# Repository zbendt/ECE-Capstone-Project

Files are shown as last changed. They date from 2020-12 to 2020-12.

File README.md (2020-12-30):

# ECE44x_Senior_Design
ECE 441 - 443 Project folder with files for senior capstone project for Jorian Bruslind, Mack Hall, and Zach Bendt

Brief descriptions of each member's responsibilities are detailed here. Below is a list of main projects for each team: 

- [**Electrical**](https://github.com/Jbruslind/ECE44x_Senior_Design/tree/master/Electrical)
	- [Stepper Driver PCB](https://github.com/Jbruslind/ECE44x_Senior_Design/tree/master/Electrical/Auxiliary%20Stepper%20Driver%20PCB)

	- [Central Processor PCB](https://github.com/Jbruslind/ECE44x_Senior_Design/tree/master/Electrical/Central%20Procesing%20PCB)

	- [Vaccumn Pump Controller](https://github.com/Jbruslind/ECE44x_Senior_Design/tree/master/Electrical/Vacuum%20Pump)

- [**Mechanical**](https://github.com/Jbruslind/ECE44x_Senior_Design/tree/master/Mechanical) 
	- [Custom Mechanical Parts/Models](https://github.com/Jbruslind/ECE44x_Senior_Design/tree/master/Mechanical/Project%20Model%20Files/Inventor%20Files/Custom_Delta)
	
	- [PCB Modeling](https://github.com/Jbruslind/ECE44x_Senior_Design/tree/master/Mechanical/Delta%20Robot%20Arm)
 
- [**Computer Science**](https://github.com/Jbruslind/ECE44x_Senior_Design/tree/master/Computer%20Science)
	- [Main Program](https://github.com/Jbruslind/ECE44x_Senior_Design/tree/master/Computer%20Science/MircobialAnalysisTool)
	
	- [GRBL Code](https://github.com/Jbruslind/ECE44x_Senior_Design/tree/master/Computer%20Science/GRBL%20Code)

Automated Microbial Analysis 

The Automated Microbial Analysis project aims to develop a system which is able to analyze a series of microbial samples on a special media 
called PetriFilm automatically. PetriFilm is a 3M product that is used in a variety of scientific capacities, mainly in food science and the medical field. 

<!---![PetriFilm](https://github.com/Jbruslind/ECE44x_Senior_Design/blob/master/Research/Petrifilm.jpg){ width=50% }-->


PetriFilm is a very thin paper-like substance which has 2 layers: on one there is an agar media film that is used to grow bacterium, 
on the other there is a wax coating that is used to seal the sample from outside interference. A liquid sample can be applied to this 
agar film and left to incubate over a period of 1 - 2 days. After this time, the bacteria that were present within the sample will have 
 had enough time to grow into colonies which are visible to the human eye. These colonies can be counted and the original number of bacterium 
 per unit volume can be known from the original sample. The process to count the bacteria samples and categorize them into datasets is often 
 tedious and can take a human operator around 1 - 2 minutes per sample. With sample sizes of 50 - 60, this process 
 can easily take over an hour. The goal of our project is to use an automated system to count these bacteria colonies in sample sets of upwards 
 of 100+ in as little as 20 minutes. This data will be automatically stored and tabulated within the client's original database. 

Being a robotics project there are inherent complexities that must be resolved between subgroups such as the electrical control of the mechanical design, 
computer commands for electrical control and how effective the mechanical design facilitates the overall process. With that, the project must maintain 
a high level of communication and simplicity so that all groups are able to understand how their design affects the overall system and others work.

### Mechanical Sub-System 

The mechanical sub-system was designed using industrial examples of delta robots in mind and special attention paid to the accuracy, speed, and cost of 
the system. Arguably, the most important aspect of our project is that is must be accurate so as not to damage the provided samples 
and to improve it's overall time cost for this process (less mistakes mean less time needed to recover). The delta robot design was made using 
many commercial off the shelf (COTS) parts with a few custom designed parts that were manufactured using a 3D printer (the Creality Ender 3 .4mm to be precise). 



### Electrical Sub-System 

The system interacts with the samples to be tested via an end-effector that is moved by three stepper motors in a delta configuration. 
The goal of the Electrical Sub-System is to enable these interactions to happen at the command of the Computer Science Sub-System. The 
stepper motors are being controlled via an ATmega 328 microcontroller. The microcontroller is running specialized software which translates 
coordinates sent from a Raspberry Pi into waveforms representing the direction, distance, and speed a motor should move in. These waveforms 
are then passed to a stepper driver, which switches power to the motor according to the information within these waveforms. The end result is a 
stepper motor which can be controlled via a Raspberry Pi. An additional ATmega 328 microcontroller is utilized to control the other electrical aspects 
of the system as well. Such duties include enabling and disabling the vacuum pump, as well as enabling and disabling the flash for the system camera.

### Computer Science Sub-System
<p align="middle">
              
</p>
The computer science sub-system has three primary functions: automation control, computer vision image analysis and user interface.
 All three of these functions are implemented on the RaspberryPi microcontroller. The user interface was created using PyQT and is used to input various pieces of data 
 such as how many samples are to be analyzed and also where the user starts/stops/resets the analysis process. The user interface is updated
 throughout the process and displays the current sample image as well as relevant data about the sample. The automation controls are calculated 
 by the RaspberryPi which then sends the control messages via serial interface to the ATmega328 where they are decoded and used to set the motors 
 to the proper angles. The image analysis is handled using OpenCV and can analyze approximately 5 samples per minute. It counts the number of microbial
 growths if any are present. After the data has been collected it is output to a .csv file that is easily transferred into a spreadsheet report.

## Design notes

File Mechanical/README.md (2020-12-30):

#	Mechanical Files 

This directory contains all the information about the mechanical design of the project and the relevant files. A good ~90% of the modeling was done by the team itself, with a few models taken from online distributors or GrabCAD (great site, definitely should check it out). All the modeling was done using AutoDesk Inventor and are arranged into .ipt part files which go into .iam assembly files.

The file structure goes as: 

- Delta Robot Arm
	- PCB Files
		- End Effector Files
		- Main Board Files
		- Stepper Motor Board Files
- Project Model Files
	- Inventor Files
	- PetriFilm Model

Almost all of the work within this sub-group is contained in the Inventor Files directory.

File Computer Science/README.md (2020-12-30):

Computer Science

Development: Old versions of code that were used during development.

GRBL Code: Code for stepper motor driver controller

Images: Images for README's

MicrobialAnalysisTool: Contains the source code for the MicrobialAnalysisTool software.

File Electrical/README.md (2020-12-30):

# Subsystem Overview

The system interacts with the samples to be tested via an end-effector that is moved by three stepper motors in a delta configuration. The goal of the Electrical Sub-System is to enable these interactions to happen at the command of the Computer Science Sub-System. The stepper motors are being controlled via an ATmega 328 microcontroller. The microcontroller is running specialized software which translates coordinates sent from a Raspberry Pi into waveforms representing the direction, distance, and speed a motor should move in. These waveforms are then passed to a stepper driver, which switches power to the motor according to the information within these waveforms. The end result is a stepper motor which can be controlled via a Raspberry Pi. An additional ATmega 328 microcontroller is utilized to control the other electrical aspects of the system as well. Such duties include enabling and disabling the vacuum pump, as well as enabling and disabling the flash for the system camera. 

## [Auxiliary Stepper Driver PCB](https://github.com/Jbruslind/ECE44x_Senior_Design/tree/master/Electrical/Auxiliary%20Stepper%20Driver%20PCB)

AUX_PCB

## [Central Processing PCB](https://github.com/Jbruslind/ECE44x_Senior_Design/tree/master/Electrical/Central%20Procesing%20PCB)

Central_PCB

## [Vacuum Pump](https://github.com/Jbruslind/ECE44x_Senior_Design/tree/master/Electrical/Vacuum%20Pump)

Vacuum_Pump

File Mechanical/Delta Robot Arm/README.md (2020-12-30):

#	PCB Files

This directory contains all of the PCB related files for manufacturing, documentation, and 3D modeling. All of these files were generated using CircuitMaker's built-in "generate outputs" function, which allows for the generation of schematics, PCB print files, 3D Step files, and Gerber files (for PCB manufacturing). 

The layout for the subdirectories is fairly simple. Within each main file there contains a list of outputs ordered as: 

## BOM

This is a generated Bill of Materials (BOM) that contains a list of all the CircuitMaker components used. This can sometimes not be very accurate due to the fact that crosslisting actual components with the built in CircuitMaker libaries can be difficult. Sometimes the various passive components used could be different values or different types. For example, we may reuse a 20uF capacitor model, but change the value to 10uF. The reason being is that it would take up too much time to individually go through all the components, footprints, and specifications for each component and source them through digikey or some other distributor. Instead, we know what we need and we just quickly put something that's the same footprint/type on the schematic and sort out the details later. The ICs or other more specific parts are almost always sourced directly however (so any chips or specialized component can be trusted, just not simple passives)  

In the end we kinda shoot ourselves in the foot for documentation purposes later, but the time saved makes it worth it (for the most part). Just a heads-up if anyone uses these files later, the actual components should be taken with a grain of salt. 

## ExportSTEP

Luckily for our mechanical designer, CircuitMaker has a built in function that will export a STEP file of the circuit board that is populated with all the components in the exact positions they're in (so long as the components are matched with a 3D model within the CircuitMaker library). 

This directory contains that exported step (and a generated .ipt version for our own modeling purposes).   

## Geber

PCB Manufacturers need a specialized set of files in order to actually manufacture the PCBs. One such set of files are called "Gerber Files". These contain the layer information for the specific circuit board such as the copper placement on the top/bottom or middle layers (depending on how many layers are present) as well as information on the hole placement, where soldermask should/shouldn't be placed, where the outline of the board is, where any board cutouts should be. Here's a brief description of each file type: 

- .GBL - Gerber Bottom Layer (copper placement on bottom layer)
- .GBO - Gerber Bottom Overlay (the text overlay on the bottom layer)
- .GBS - Gerber Bottom Solder (where the bottom solder mask should be placed)
- .GPB - Gerber Bottom Paste (where solder paste should be - almost never used by us) 
- .GTL - Gerber Top Layer (copper placement on top layer)
- .GTO - Gerber Top Overlay (the text overlay on the top layer)
- .GTS - Gerber Top Solder (where the top solder mask should be placed)
- .GTB - Gerber Top Paste (where solder paste should be - almost never used by us) 
- .GKO - Gerber Keep Out (what the PCB manufacturer's shouldn't touch - we use this as an outline for our board) 

Everything else pretty much isn't used by us. 

## Manufacturing Files 

These contain all the files that we *actually* need to manufacture the PCB (what we send to the factory). 

- .GBL
- .GBO
- .GBS
- .GTL
- .GTO
- .GTS
- .GKO
- .XLN - This is a special file for drilling

In this directory you'll find all these files and a .zip folder containing them which you can use to send to a factory for PCB manufacture. 

## NC Drill

This directory has the drilling outputs for the specific PCB. This will include information on what hole should be placed and where. There is a specific file in here that usually has the structure "projectname.txt", this file has all the CNC commands to actually route the holes for the board. We take this file, rename the extension .XLN and combine it with our other gerber's for manufacture (not sure why, we've just always done it and it works) 

## *"projectname".pdf* 

This pdf has all the information about the circuit board such as schematics and PCB layout. You can find all the details about the specific project in this.

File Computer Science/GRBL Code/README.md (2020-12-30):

# GRBL Code

This project utilizes [GRBL](https://github.com/grbl/grbl), which is an open-source stepper motor driver controller designed to run natively on an Arduino Uno. However, the Arduino Nano has the same number of digital output pins as the Arduino Uno, so it is possible to modify the code to run on the Nano.

The Arduino Nano barely has enough memory to flash grbl on to it, but it does. From there, the cpu_map.h file needs to be modified, in order to redirect the output signals to the proper pins. For our case, the signals were redirected to the following pins:

[GrblNanoPinout](https://github.com/Jbruslind/ECE44x_Senior_Design/blob/master/Code/GRBL%20Code/GrblNanoPinout.PNG)

Every other part of grbl is unmodified, aside from a few grbl settings used for smoother operation. Such settings are set as follows:

|Setting|Value|
|----|----|
|$0|10|
|$1|255|
|$2|0|
|$3|7|
|$4|0|
|$5|0|
|$6|0|
|$10|1|
|$11|0.010|
|$12|0.002|
|$13|0|
|$20|0|
|$21|0|
|$22|0|
|$23|0|
|$24|25.000|
|$25|500.000|
|$26|250|
|$27|1.000|
|$30|1000|
|$31|0|
|$32|0|
|$100|250.000|
|$101|250.000|
|$102|250.000|
|$110|500.000|
|$111|500.000|
|$112|500.000|
|$120|10.000|
|$121|10.000|
|$122|10.000|
|$130|300.000|
|$131|300.000|
|$132|300.000|

Since both the Arduino Uno and Arduino Nano utilize the ATmega 328 microcontroller, that was a large determining factor as to why we chose it to use it for this project.

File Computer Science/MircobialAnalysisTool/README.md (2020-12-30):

GUI.py - User interface source code
The bulk of the design and layout portion of this module was auto generated using QtDesigner then modified to fit our purposes.
The GUI has two threads running simultaneously. One updates the image that is displayed as well as the sample data. The other handles the automation controls and image analysis.

deltaImageProcessor.py - Handles image capture, and data output to .csv file.

colonyCounter.py - Computer Vision analysis
This module takes in a file from the "/images" folder located in the current working directory, performs computer vision analysis and applies keypoints over any detected colonies.

robo_controls.py – Sends automation control messages.
This module sends automation control messages via serial interface to the ATmega328 where they are decoded and used to set the motor anagles.

### User Interface

The GUI was developed using [PyQt5](https://pypi.org/project/PyQt5/). First, [QtDesigner](https://pythonbasics.org/qt-designer-python/) was used to build the basic layout, such as button and label placement placement.

<p align="middle">
   
</p>

Most of the placement of buttons and labels are self explainitory. In order to display the image it has has to displayed in a QLabel feature.

<p align="middle">
   
</p>

Once the basic layout was set, QtDesigner exported a .ui file. This is then converted into editable code using a program called [pyuic5](https://pypi.org/project/pyuic5-tool/)

This gave a baseline for the GUI and we were then able to implement the fucntions that we need the GUI to perform. We were able to implement PyQt [QThreadPools](https://doc.qt.io/qt-5/qthreadpool.html) the let the GUI update with current image and other relevenat sample data. All threading was based on [this tutorial](https://www.learnpyqt.com/courses/concurrent-execution/multithreading-pyqt-applications-qthreadpool/)

### Computer Vision 

The basics of the computer vision was based on [this tutorial](https://www.learnopencv.com/blob-detection-using-opencv-python-c/). Though we were not able to fully implement the computer vision system due to the COVID19 global health crisis, the provided is a starting point to begin fine tuning the computer vision system.

The computer vision system follows these basic steps:
1. Capture image.
2. Convert image to grayscale.
3. Run analysis based on certain parameters (a full explaination of the parameters can be found in the linked tutorial).

<p align="middle">
   
</p>

4. Keep count of microbial colony growthsd
5. Place keypoints on image over detected microbal colony growths.
6. Output the image with keypoints to the designated directory so it can be dislpayed on the GUI.
7. Output relevenat sample data to a .csv file.

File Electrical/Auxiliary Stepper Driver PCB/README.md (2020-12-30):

# Stepper Driver PCB

This PCB acts as a link between the Primary Control PCB and the stepper motors themselves. Since there are three stepper motors, there will be three separate instances of this PCB in the final system. This PCB takes in a signal from one of the ATMEGA328s on the Primary Control PCB, and outputs another electrical signal which will turn the stepper motors. In order to verify that this PCB is working correctly, there are status LEDs for 24V and 5V power, as well as status LEDs for RX and TX packets.

PCB
PCB_Bottom
PCB_LayerTop
PCB_LayerBottom

## Ethernet Port

The Auxiliary Driver PCB accepts its input from the Central Processing PCBs in the form of an ethernet cable. The ethernet cable carries 24VDC, a direction signal, a step signal, and RX and TX lines for serial communication. The ethernet cable was chosen due to its ubiquity and low cost. Four pins in total are dedicated to power delivery, while the other four pins are dedicated to other signals.

EthernetNet
Ethernet

## Stepper Motor Connection

J2, a Phoenix Contact 1803293, is the connector for the stepper motor itself. The connector is compatible with the stepper motors we already had as a group, and were chosen as a result. This connector is capable of handling up to 8A. Since the motors themselves only use up to 2A maximum at a time, this has a safety factor of 400%. 

MotorNet
Motor

## Encoder Connector and Signal Processing

J3, a TE Connectivity / AMP 5747844-4, is the DB9 connector used to interface with the encoder integrated on the stepper motor itself. The DB9 connector allows the encoder signal to be read in by the ATtiny85 (U2 on the PCB), where the signal is interpreted. Finally, the motor position is sent back to the Central Processing PCB along the ethernet cable via serial communication. This allows the software to know where the motors are physically at all times. This allows a greater degree of control, because the motors may occasionally “miss” a step and become misaligned with their intended position. The encoder signal allows us to detect this and either compensate for this error on the software side of things or completely re-home the system altogether. Missing a step typically only occurs at higher speeds, and our motors are run at relatively low speeds, so it should not come up too often, but it is always good to prepare for the worst. 

Attiny85
DB9_Net
ATtiny85_and_DB9

## Voltage Regulation

X1 is a Texas Instruments LMZM23601V5SILT buck converter which converts the 24VDC line to a 5VDC line for use on the Auxiliary Driver PCB. The 5V line is used to power the stepper driver, the encoder, the Attiny85, and the RX, TX, and 5V status LEDs. The LMZM23601V5SILT is rated for up to 1A of use, but the auxiliary current the Auxiliary Driver PCB draws is much less than that in reality.

VoltageRegulatorNet
VoltageRegulator

## Stepper Drivers

J8-L and J8-R are sockets for where a stepper driver daughterboard (a.k.a. stepstick) could connect. Although it can be used for testing and debugging purposes, this socket is not to be  used in the final system, as all microcontrollers under 64 pins must be soldered directly on the PCB. On the opposite side of the PCB, there is a place to solder an SMD stepper driver chip (U1 on the PCB). We chose to go with the Trinamic TMC2209 due to its low cost and high reliability. The TMC2209 is capable of handling up to 2.2 A per stepper motor, which is below our peak of 2 A. The stepper driver will have a heatsink in addition in order to help dissipate heat and ensure high performance over extended operational periods. 

StepperDriverNet
StepperDriverSocket
TMC2209

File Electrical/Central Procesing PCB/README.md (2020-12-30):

# Central Processing PCB

This PCB handles everything related to driving the motors from a software point of view. It interprets the motor coordinates sent from the Raspberry Pi, sends signals and power to the Auxiliary PCBs, and processes encoder data from the motors. 

CentralPCB
CentralPCBBottom
PCB_TopLayer
PCB_BottomLayer

## Ethernet Connectors

The Auxiliary Driver PCB accepts its input from the Central Processing PCBs in the form of an ethernet cable. The ethernet cable carries 24VDC, a direction signal, a step signal, and RX and TX lines for serial communication. The ethernet cable was chosen due to its ubiquity and low cost. Four pins in total are dedicated to power delivery, while the other four pins are dedicated to other signals. Since the Central Processing PCB has to control three separate Auxiliary Diver PCBs, the Central board has three ethernet ports (J3, J4, & J5), one for each Auxiliary PCB. 

EthernetNet
Ethernet

## Power Conversion and Distribution

The Central Processing PCB distributes power to the rest of the system from the external power supply. The board takes in power from J0, a male XT30 connector, which is rated up to 30A as the name implies. The power supply itself that we are using is rated for only 20A, so this is a non-issue. 

ConNet
Connector

The Central Processing PCB also requires a fairly robust 5VDC converter, since it is responsible for powering the Raspberry Pi as well as two ATMEGA328 microcontrollers. As such, the PCB utilizes the Bel Fuse SRBH-06H1A1R (U3 on the PCB \[missing a 3D model]), which is capable of stepping down a 24VDC input into a 5VDC output up to 6A. This is overkill for our system, as each of the listed components that draw from the SRBH-06H1A1R only take about 1A each. As such, we have a safety factor of 100%.

RegulatorNet
Regulator

As mentioned above, the Central PCB provides 5VDC to the Raspberry Pi via its GPIO pins. This is not recommended by the makers of the Raspberry Pi, as the GPIO pins bypass the internal fusing and regulation done in order to ensure a safe and regulated 5V line for the system. Before going to the upside-down headers that allow the Central PCB to be worn as a Raspberry Pi hat, the 5V line on the Central PCB must go through a resettable thermal fuse (F1 on the PCB) in order to ensure that the Raspberry Pi cannot draw enough current to harm itself. The fuse we are using is the Bel Fuse 0ZCH0200FF2E, which is rated for 2A before tripping. Once tripped, the fuse will reset after being returned to room temperature.

RPiNet
RPi

Furthermore, the Central PCB is also responsible for providing 12VDC to drive the vacuum pump. The vacuum pump simply turns on when a voltage is applied to the terminals. Therefore, the system will utilize a relay to turn the pump on and off. The schematic is as shown:

RegulatorNet

The 12VDC line is supplied by U1, a Cyntec MUN24AD03-SM, which is a simple buck converter that steps down a 24VDC signal to a 12VDC signal. The 24VDC signal is the “common” DC-bus throughout the system, which means it is supplied from an external load-regulating power supply that rectifies wall voltage. The Cyntec MUN24AD03-SM is capable of handling up to 3A, and is therefore more than plenty for our vacuum pump, which only draws 1A at maximum. 

VoltageRegulator

## Vacuum Pump

On the Auxiliary ATmega 328 found on the Central PCB, the enable pin of the K1 relay is tied to PD4 (physical pin 2), which is capable of sending a 5VDC signal to open or close the relay. When the K1 relay is open, the RELAYED_VACUUM_PUMP_12V net, which is connected to the positive terminal of the vacuum pump, is left floating, meaning the vacuum pump is getting no voltage and is therefore off. When the K1 relay is closed, the RELAYED_VACUUM_PUMP_12V net receives 12VDC and turns the pump on.  

Relay

The D2028 vacuum pump is connected to the Primary Control PCB via the P5 header. 

ConnectorNet
Connector

## Camera Flash

The K2 relay is responsible for enabling the LEDs below the camera, in order to act as a flash. These LEDs take a 5V input, and are therefore tied to the 5V regulated line on the board. This setup is very similar to the vacuum pump, however it is only 5VDC instead of 12VDC. 

FlashRelayNet
FlashRelay

## Onboard Microcontrollers

The Central PCB also needs to connect all of the prior connections to two ATmega 328 microcontrollers, which will actually run the software we need to control the system. The PCB includes sockets to plop in two Arduino Nanos for testing and debugging purposes, but this will not be used in the final system. The back of the PCB hides the solder pads for two SMD ATmega 328s (AUX_ and Stepper_ on the PCB), as well as two external 16MHz clocks (X1 and X2), and two 5V regulators (Q1 and Q2).

ArduinoA
ArduinoB
ArduinoC

Essentially, the PCB has the equivalent hardware of two integrated Arduino Nanos on board. They have the equivalent connections lifted straight from the official Nano schematic itself found [here](https://www.arduino.cc/en/uploads/Main/Arduino_Nano-Rev3.2-SCH.pdf).

The Stepper_ ATMEGA 328 is responsible for running a program called ‘grbl’. grbl is a well-established software that is used for driving stepper motors. The user inputs G-Code, and grbl will generate the equivalent signals to be sent to the stepper motor driver that will move the motor to the coordinates defined in said G-Code. Essentially, the stepper driver is a median in which grbl can move the stepper motor directly. Along with other signals, the necessary signals generated from grbl are sent through the ethernet cable, where they are eventually interpreted by the TCM2209 on the Auxiliary Diver PCB. In the final system, the Raspberry Pi will be running a script which will send G-Code serially to the Stepper_ ATMEGA, which will control the position of the stepper motors indirectly via the stepper motor divers. 

The AUX_ ATMEGA 328 is responsible for reading back the messages sent by the Auxiliary Stepper PCBs, as well as turning on the relays for the vacuum pump and the camera flash. An additional ATMEGA 328 was used in conjunction with the Stepper_ ATMEGA 328 due to computational bottlenecks. grbl is a very demanding program, and attempting to run additional code could impact the timing of the wave generation, meaning that the end stepper motor motion would not be as accurate or as smooth.

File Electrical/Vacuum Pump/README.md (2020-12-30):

# Vacuum Pump

This vacuum pump is used to create suction in order to pick up the cultural samples. It is controlled via a relay located on the primary control PCB. The D2028 is very common among enthusiasts, and with good reason: this budget motor is dead simple, reliable, and effective. 16” of mercury over a ¼” diameter suction cup means this pump can theoretically lift a little over ⅓ of a pound, which is plenty for our application, as its load weighs only ~100 g. This allows for a safety factor of ~50%.

VacuumPump
Datasheet

## Vacuum Pump Relay

The vacuum pump simply turns on when a voltage is applied to the terminals. Therefore, the system will utilize a relay to turn the pump on and off. The schematic is as shown:

RelayNet

On the Auxiliary ATMEGA328 found on the Central PCB, the enable pin of the K1 relay is tied to PD4 (physical pin 2), which is capable of sending a 5VDC signal to open or close the relay. When the K1 relay is open, the RELAYED_VACUUM_PUMP_12V net, which is connected to the positive terminal of the vacuum pump, is left floating, meaning the vacuum pump is getting no voltage and is therefore off. When the K1 relay is closed, the RELAYED_VACUUM_PUMP_12V net receives 12VDC and turns the pump on.  

Relay

## Voltage Regulator

The 12VDC line is supplied by U1, a Cyntec MUN24AD03-SM, which is a simple buck converter that steps down a 24VDC signal to a 12VDC signal. The 24VDC signal is the “common” DC-bus throughout the system, which means it is supplied from an external load-regulating power supply that rectifies wall voltage. The Cyntec MUN24AD03-SM is capable of handling up to 3A, and is therefore more than plenty for our vacuum pump, which only draws 1A at maximum. 

VoltageRegulator
RegulatorNet

## Connector

The D2028 vacuum pump is connected to the Primary Control PCB via the P5 header. 

ConnectorNet
Connector

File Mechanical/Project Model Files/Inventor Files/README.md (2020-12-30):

#	Inventor Files

For this project there was quite a few custom designed mechanical structures that were needed. These included small things like simple fasteners or mounts to 
more complex components, like a 3 point motor mounting platform and electrical covers. Each directory is named for the parts it contains and we have sorted
the parts by source to try and give some organization to the overall directory. For example, parts that are sourced externally (bought or given) from 
a site such as McMaster Carr are sorted into the McMaster directory. Simple parts such as bolts, nuts, etc are not sourced explicitly (because they are 
so prevalent) and are instead just placed into a general directory called "Metric Bolts" or "Metric Nuts" 

Below is a general description of the different directories and what they contain 

## Custom Delta

This directory contains all of the custom made components for the current revision of the Delta robot. All of the files contained in this directory have 
been custom made/designed/modeled by Jorian Bruslind. 

## Delta Bot

This directory contains the original file for a base model Delta robot designed by daGHIZmo on Thingiverse. We used this as a model reference to see 
how a Delta robot looks like using 3D printed components. I highly recommend to check out his thingiverse profile, it has got some great stuff

Link here

## McMaster Files

We purchased most of our mechanical system from McMaster Carr as they had the best selection and prices for easy to use fasteners/material. Each file 
contained in this directory has the McMaster part number as a prefix in its name (for easy reference). 

## Digikey Files

We also purchased quite a few parts from digikey although these were more electrically related than mechanical. The mechanical parts that were purchased 
were mostly connectors to interface with the stepper motors we purchased. In addition this directory also contains a model for the Raspberry PI 4 and 
Raspberry Pi Camera v2.0 (both were used in the system). 

## Sparkfun Files 

The only component actually bought from Sparkfun was a stepper shaft collar that allowed easy mounting access for our armatures. The step file (and ipt file) 
for this is contained in this directory. 

## Metric Nuts/Bolts

For this project we tried to maintain metric as our standard measurement of choice due to its ubiquity in engineering and ease of use (simple, rounded numbers). 
As such we have a general repository of metric bolts/nuts that we used in our models. This section does not have a specific supplier because we bought 
these parts from various suppliers (Amazon, McMaster, local hardware stores, etc)

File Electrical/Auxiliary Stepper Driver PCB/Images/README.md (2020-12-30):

This folder is used to hold images used in the Auxiliary Stepper Driver PCB README.md

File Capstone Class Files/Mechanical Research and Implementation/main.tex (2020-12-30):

\documentclass[11pt]{article}

%% Language and font encodings
\usepackage[english]{babel}
\usepackage[utf8x]{inputenc}
\usepackage[T1]{fontenc}
\usepackage[section]{placeins}
\usepackage{graphicx}
\usepackage{caption}
\usepackage{subcaption}
\usepackage{float}
\usepackage{verbatim}
\usepackage{color,soul}
\usepackage{indentfirst}
\usepackage{listings}
\usepackage{fancyhdr}
\usepackage{sectsty}
\sectionfont{\centering}
\usepackage{abstract}
\usepackage{vhistory}
\renewcommand{\abstractnamefont}{\normalfont\Large\bfseries}
%% Sets page size and margins
\usepackage[a4paper,top=3cm,bottom=1cm,left=1cm,right=1cm]{geometry}

%% Useful packages
\usepackage{amsmath}
\usepackage[colorinlistoftodos]{todonotes}
\usepackage[colorlinks=true, allcolors=blue]{hyperref}
\usepackage{listings}
\usepackage{color} %red, green, blue, yellow, cyan, magenta, black, white
\definecolor{mygreen}{RGB}{28,172,0} % color values Red, Green, Blue
\definecolor{mylilas}{RGB}{170,55,241}
\setlength{\parindent}{2em}
\setlength{\parskip}{.75em}

\date{\today}

\begin{document}

\begin{titlepage}
	\centering
    \begin{minipage}{0.05\textwidth}

    \end{minipage}
    \rule[-400pt]{1.5pt}{600pt}
    \hspace*{0.05\textwidth} % Whitespace between the vertical line and title page text
    \begin{minipage}{0.5\textwidth}
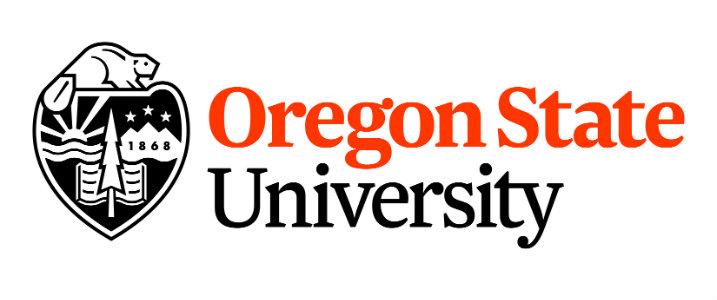
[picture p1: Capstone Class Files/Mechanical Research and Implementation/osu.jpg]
        \par\vspace{1cm}
        \vspace{.5cm}
    	{\scshape\Large ECE 44x - Group 3  \par Automated Microbial Analysis\par}
    	\vspace{1cm}
    	{\huge\bfseries Reading and Implications Report \par}
    	{\large\bfseries Mechanical Design - Connectors and Enclosures \par}
    	\vspace{1cm}
    	{\Large\itshape Jorian Bruslind\par}

	    \vspace{1cm}
    \vspace{.25cm}
    \end{minipage}

% Bottom of the page
	{\large \today\par}
\end{titlepage}
\newgeometry{top=2.5cm,bottom=2.5cm,right=2cm,left=2cm}
\tableofcontents

\newpage

\pagestyle{fancy}
\fancyhf{}
\rhead{Automated Microbial Analysis}
\lhead{Mechanical Design}
\rfoot{Page \thepage}

\begin{abstract}
    The purpose of this document is to provide context for the reader behind the design choices made within the perview of the mechanical design aspect of the Automated Microbial Analysis capstone project. This project aims to manipulate, analyze, and physically sort microbial samples present on 3M Petrifilm. This document will cover the mechanical concepts present in the system, the design choices for each concept and the proposed solution for each choice. Finally, this document will then cover the expected challenges with this project and possible solutions to said challenges. 
\end{abstract}

\section{Introduction}

The Automated Microbial Analysis project aims to develop a system which is able to analyze a series of microbial samples on a special media called PetriFilm \cite{beveragedaily.com2014May} automatically. This is a 3M product that is used in a variety of scientific capacities, mainly in food science and the medical field. 

\begin{figure}[H]
    \centering
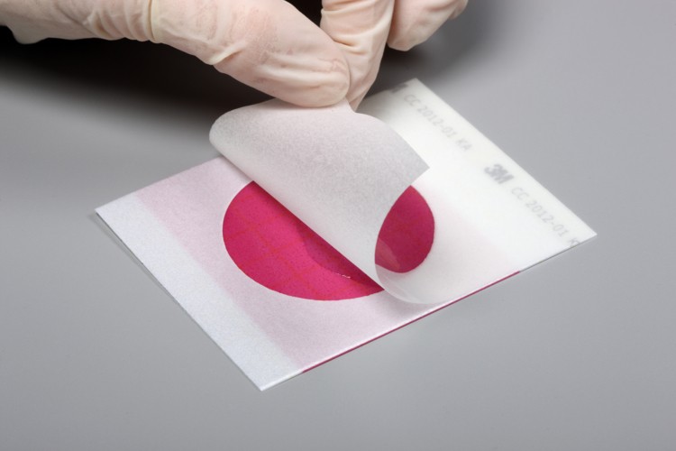
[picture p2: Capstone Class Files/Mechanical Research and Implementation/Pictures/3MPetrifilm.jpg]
    
    \caption{3M PetriFilm Single Sample}
    \label{fig:Petrifilm}
\end{figure}

PetriFilm is a very thin paper-like substance which has 2 layers: on one there is an agar media film that is used to grow bacterium, On the other there is a wax coating that is used to seal the sample from outside interference. A liquid sample can be applied to this agar film and left to incubate over a period of 1 - 2 days. After this time, the bacteria that were present within the sample will have  had enough time to grow into colonies which are visible to the human eye. These colonies can be counted and the original number of bacterium per unit volume can be known from the original sample. The process to count the bacteria samples and categorize them into datasets is often tedious and can take a human operator around 1 - 2 minutes per sample \cite{3M_Interpretation}. With sample sizes of 50 - 60, this process can easily take over an hour. The goal of our project is to use an automated system to count these bacteria colonies in sample sets of upwards of 100+ in as little as 20 minutes. This data will be automatically stored and tabulated within the client's original database. 

For this process it is necessary to create a physical manipulation system that will be able to move paper-like objects in an efficient and precise manner. These samples are somewhat delicate and require careful handling. In addition, they must be placed in a specific orientation so that the bacterial samples can be easily read by some visual component. Therefore it is necessary to create a mechanical system that can be easily made precise and is able to be used for our intended implementation. In addition, there will be designated areas for loading/unloading of samples so that the overall process requires as little human intervention as possible.  

Once the loaded, the system will take over and begin the counting process for each sample. There will be error correction and state information for each portion of the counting cycle to ensure the samples are not damaged and to reduce the chance of a miscount. After the sample has been counted and cataloged, it will be placed into one of two sections designated "Pass" or "Needs Review" where they can be sorted by a human operator. 

This document aims to provide context for my responsibilities as they apply to the project and what steps were taken to achieve the goals outlined above. I have personally been involved in a variety of robotics related projects working with groups ranging from 1 - 20 people. I have had experience working with control systems, mechanical design, and automated systems and it is my hope that I can apply that experience towards the success of this project. 

\section{Summary of Expert Topic Areas and Design Challenges}

This project requires a great deal of mechanical, electrical and computer science engineering and necessitates the complexity of having each area work together. To help simplify the design process, each team member is assigned an area of expertise that they are responsible for. For me specifically, I will be responsible for the mechanical design and hardware implementation of our system. 

\subsection{Area of Expertise}

For this project, 2 mechanical systems came to mind that are used in similar applications. The first being a printer while the second was a pick and place machine. Both use fairly intricate mechanical systems to preform their function and as such I need to be aware of their abilities and limitations. It is important to consider parameters such as speed, simplicity in design, cost, and ease of use when designing a system such as ours and it will be my responsibility to analyze each when considering the different options. 

For this area of expertise, I will need to be responsible for the design and simulation of our mechanical system. To do so I will use Computer Assisted Design (CAD) in the form of Autodesk Inventor to model our entire system before assembly. I have had around 6 years experience working with Inventor in other applications and feel confident in it's ability for CAD modeling. 

\subsection{Design Challenges}

The project requirements that most relate to my area of expertise include: Accuracy, Sample Preservation, Fast, Enclosed Work Area, and Ease of Use. All of these requirements require the mechanical system in some way, shape or form. With this in mind my research focused on the possible mechanical systems and their ability to meet the aforementioned requirements. Speed and accuracy were the two requirements I spend the most amount of focus on as they were ultimately the most influential in deciding which mechanism to go with. In addition, most all systems can be designed in such a way to be easy to use, have an enclosed work area, and prioritizing accuracy provides a means for sample preservation. 

A focus of my research was what mechanical systems were used in industry for similar purposes to ours. The point being that many companies would have invested time and money into figuring out the most efficient way to preform their specific task. First, an analysis of the task that is to be preformed indicated 2 possible mechanisms: Pick and Placing and printing/scanning. The PetriFilm can be thought of as slips of paper in the fact that they are both light and thin. Therefore, the most common forms of industrial robotics that deal with paper-like objects are through printing/scanning mechanisms and pick/placing mechanisms \cite{robot_types}. The printing/scanning methods (as seen in \ref{fig:printer})seem to be the most ideal, considering the act of imaging paper is the same process that we must do to the PetriFilm. Within the pick and placing category, the most popular type of robots found in industry include the Delta robot configuration \ref{fig:Delta} and the Cartesian (Gantry) robot configuration \ref{fig:Gantry}. For simplicity, I will focus on the contrasts between our 3 stated requirements and the aforementioned robotic systems. 

    \begin{figure}[H]
    \centering
    \begin{subfigure}{.3\textwidth}
      \centering
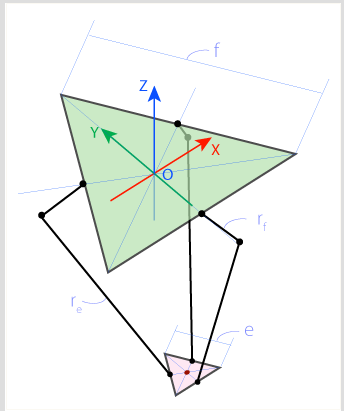
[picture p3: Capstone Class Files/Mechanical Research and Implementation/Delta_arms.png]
      
      \caption{Modeled Delta Robot)}
      \label{fig:Delta}
    \end{subfigure}%
    \begin{subfigure}{.3\textwidth}
      \centering
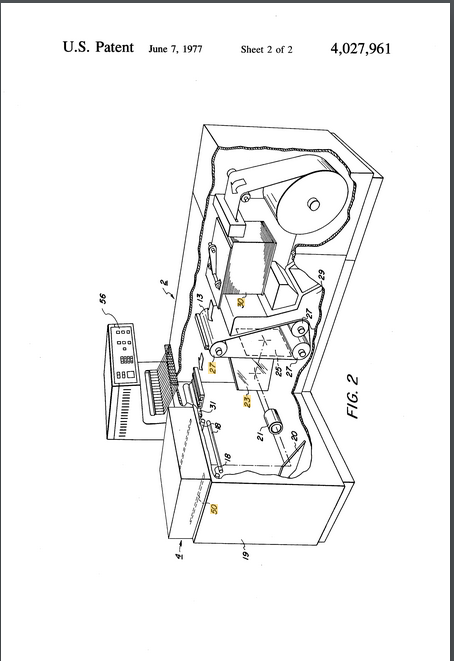
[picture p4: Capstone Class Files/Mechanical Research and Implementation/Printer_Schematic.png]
      
      \caption{Simple Printer Schematic)}
      \label{fig:printer}
    \end{subfigure}
    \label{fig:test}
    \begin{subfigure}{.3\textwidth}
      \centering
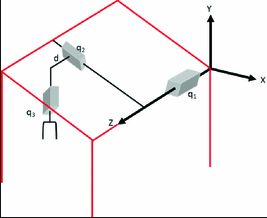
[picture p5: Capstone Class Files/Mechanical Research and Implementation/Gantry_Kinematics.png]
      
      \caption{Modeled Gantry Robot}
      \label{fig:Gantry}
    \end{subfigure}
    \label{fig:test}
    \end{figure}

%Links
%https://www.researchgate.net/publication/319876160_Mechanical_Design_of_a_Cartesian_Manipulator_for_Warehouse_Pick_and_Place - Delta Speed
%https://patents.google.com/patent/US4027961 - complex printer
%http://cms.gcg11.ac.in/attachments/article/102/Printers,types%20,working%20and%20use..pdf - Slides about printers
%https://www.plantautomation-technology.com/articles/types-of-robots-based-on-configuration - compare/contrast robots

\section{Challenge 1 - Accuracy}

Arguably, the most important aspect of our project is that is must be accurate so as not to damage the provided samples and to improve it's overall time cost for this process (less mistakes mean less time needed to recover). To measure accuracy, I investigated 2 components of the mechanical systems, the end effector accuracy and what steps are necessary to improve the end effector accuracy. The end effector in this case is whatever part is going to be moving the samples during the process. It is necessary to also investigate possible improvements to the accuracy of the systems as some systems may not have the best inherent stability, but for relatively little cost they could be improved. For simplicity, I am assuming all motors used are NEMA 17 200 step/rev 2 phase stepper motors \cite{Nema17} so as to standardize the investigation. 

\begin{figure}[H]
    \centering
    \begin{subfigure}{.4\textwidth}
        \centering
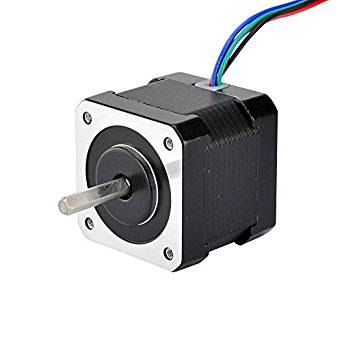
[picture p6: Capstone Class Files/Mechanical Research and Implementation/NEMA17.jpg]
        
        \caption{NEMA 17 Stepper Motor}
        \label{fig:NEMA17Step}
    \end{subfigure}
    \begin{subfigure}{.4\textwidth}
        \centering
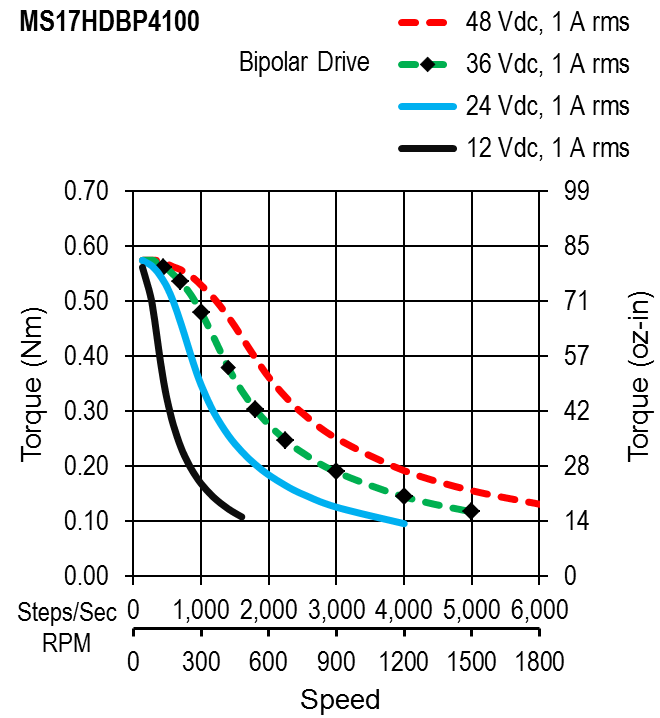
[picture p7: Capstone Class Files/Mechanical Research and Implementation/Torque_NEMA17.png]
        
        \caption{NEMA 17 Torque Curve \cite{NEMATorque}}
        \label{fig:NEMA17torque}
    \end{subfigure}
\end{figure}

If we were to model our design after a printer/scanner then it would be accurate to within a few mm, however it comes at the cost of many different sensors and a complex mechanical system. Looking at the overall design of a printer system, it can be seen that in order to facilitate the processing of samples in a stack, there must be mechanisms that keep the stack in order, in place, and restricted enough so that only 1 sample is taken at one time. It is known that printers will often experience jams or other physical problems that would ultimately destroy the samples if they occurred. So while it may be possible to achieve accuracy to a fine degree, the amount of extra work required to achieve this is beyond the scope of our ability. 

%https://mindmachine.co.uk/book/print_18_paperfeed.html

Other possible options for this design would be to employ a robotic system to manipulate samples within a set workspace. Both Gantry and Delta robots are renown for their ability or preform pick and place operations accurately. The reason for choosing pick and place for our operation is that samples can easily be put into a stack and picked off / placed down for analysis. 

Of the two options, the easiest to understand is probably the Cartesian (Gantry) robot. This mechanical system is simple in that it just uses 1 stepper to move in each Cartesian direction. Therefore the accuracy of the overall system is just limited by the accuracy of the chosen stepper motor. Depending on the operation, it may be necessary to scale the torque of the stepper motor through gear/pulley ratios which would ultimately reduce the overall accuracy \cite{Stepper_Pulley}, but for the purposes of this document we will assume there is no reduction. 

    \begin{figure}[H]
        \centering
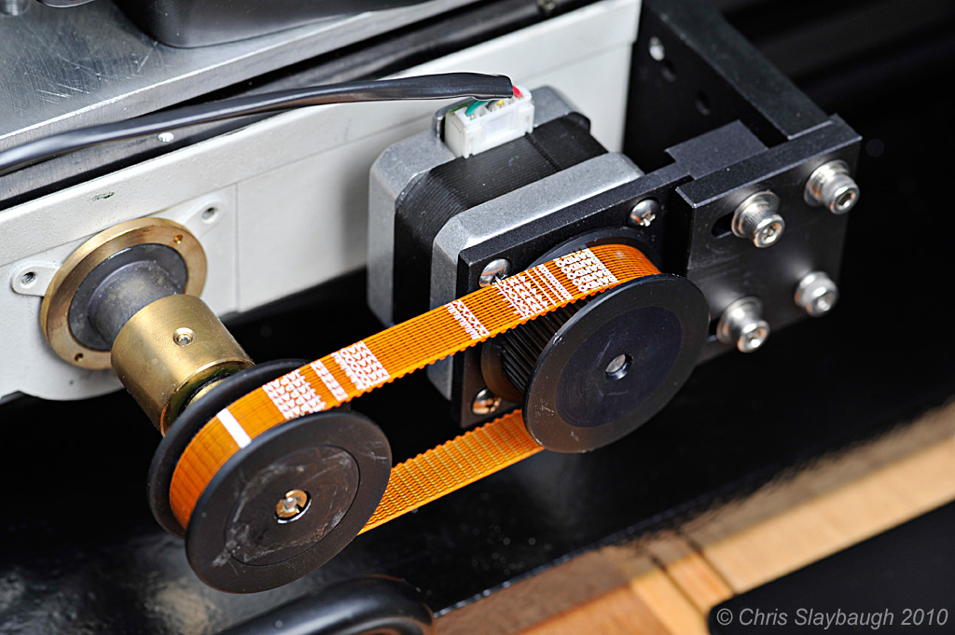
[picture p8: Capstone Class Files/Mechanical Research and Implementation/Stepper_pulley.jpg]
        
        \caption{Possible gear reduction using pulley}
        \label{fig:forward_kin}
    \end{figure}

The Delta robot is a little more complicated in the analysis of accuracy. Similar to the Gantry robot, the accuracy is directly related to the chosen stepper motors, however the error factor is multiplied by a factor related to the delta robot armature length. This is due in fact to the idea that the stepper will drive a longer arm which in turns moves the end effector. Therefore a small error on part of the rotation of the stepper, will induce a larger error (translationally) at the end of the arm length (arc length vs angle). Therefore the Delta robot will have a similar accuracy to the Gantry robot just scaled by a factor of the chosen armature length. 

    \begin{figure}[H]
    \centering
    \begin{subfigure}{.5\textwidth}
      \centering
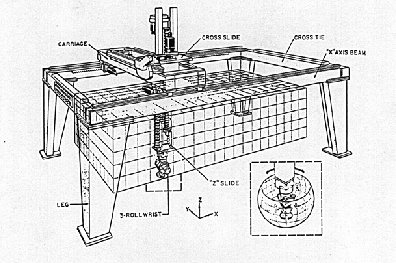
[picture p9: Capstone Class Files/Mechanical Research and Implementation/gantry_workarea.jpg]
      
      \caption{Gantry work area}
      \label{fig:Gantry_Work}
    \end{subfigure}%
    \begin{subfigure}{.5\textwidth}
      \centering
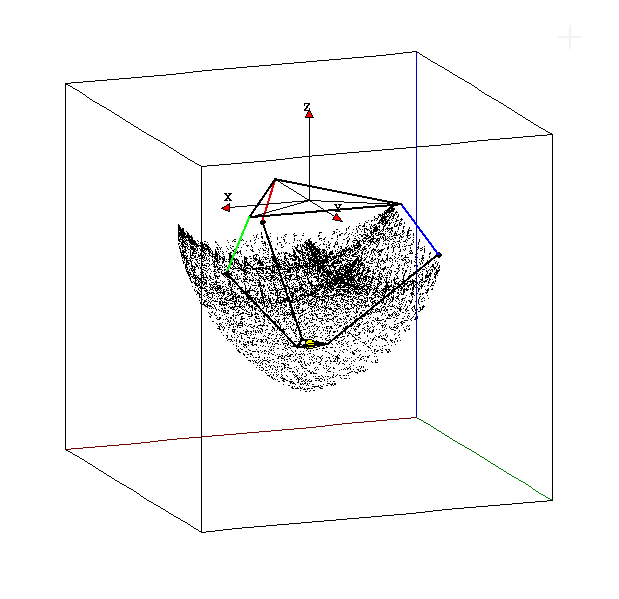
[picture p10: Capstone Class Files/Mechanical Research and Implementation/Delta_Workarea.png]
      
      \caption{Delta work area from simulation \cite{Delta_Sim}}
      \label{fig:Delta_Work}
    \end{subfigure}
    \label{fig:test}
    \end{figure}

\section{Challenge 2 - Speed}

Speed is also an important consideration for this project. while accuracy ensures the samples will not be damaged, speed is ultimately speed is why the project exists at all. In order to consider the project effective, it must be able to move samples on the order of 100 / 5 - 10 min. With this in mind, I thought of speed as very close (but not quite as) important as accuracy.  

For the Gantry robot, speed is limited to the abilities of the chosen stepper motors and the location of the sample input/output stacks \cite{Cartisian_Design}. This can be amplified through the use of gearboxes or pulley systems, with the cost of losing some torque or overall force power. 

The Delta robot is a little more complicated. The speed that this mechanism can achieve is mostly based off of its armature length as explained above. For every $1^\circ$ of rotation, the actual movement is based off the arc length which is in turn based off the length of the armature. By deriving the Delta robot's forward kinematic equations (where, given ($\Theta_1, \Theta_2, \Theta_3$) we can determine ($X_0, Y_0, Z_0$)), it is possible to determine by what factor the actual speed is increased. Using the model variables found in \ref{fig:Delta_Label} the derivation follows between images \cite{TrossenRobotics}.

    \begin{figure}[H]
    \centering
    \begin{subfigure}{.5\textwidth}
      \centering
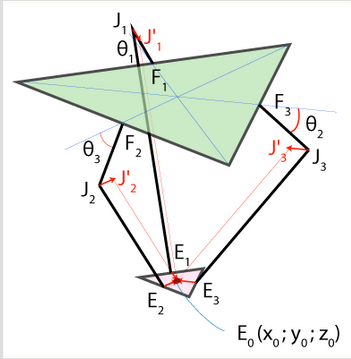
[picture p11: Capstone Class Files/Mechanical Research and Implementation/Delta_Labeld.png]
      
      \caption{Labeled Delta Variables}
      \label{fig:Delta_Label}
    \end{subfigure}%
    \begin{subfigure}{.5\textwidth}
      \centering
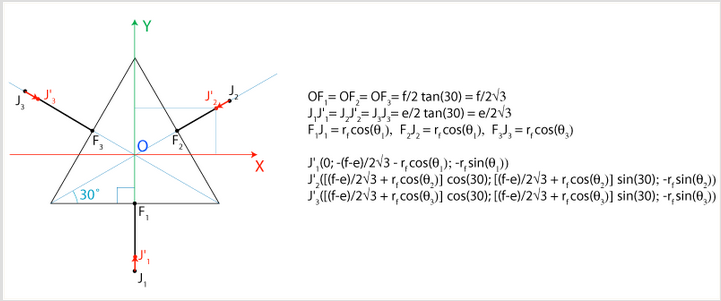
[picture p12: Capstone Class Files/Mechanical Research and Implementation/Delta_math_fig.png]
      
      \caption{Defining Delta parameters with corresponding equations}
      \label{fig:Delta_math_fig}
    \end{subfigure}
    \label{fig:test}
    \end{figure}
    
    \begin{figure}[H]
        \centering
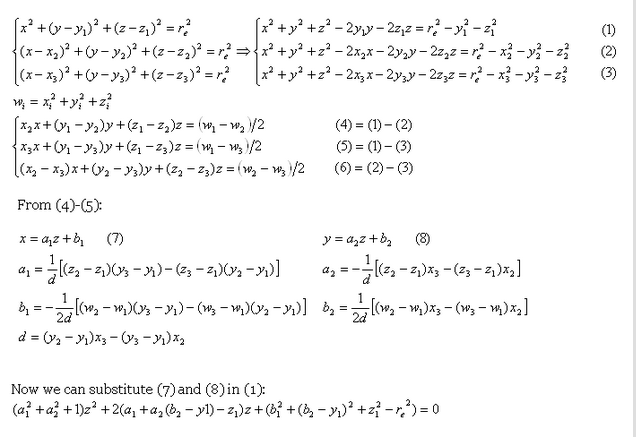
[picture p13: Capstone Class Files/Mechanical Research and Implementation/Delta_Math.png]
        
        \caption{Forward Kinematics calculations}
        \label{fig:forward_kin}
    \end{figure}
    
Generalizing from \ref{fig:forward_kin} we can determine that the rotation of all 3 motors $1^\circ$ would increase the Z axis parameter by a factor of $cos(\theta) \cdot F_x$ where $F_x$ is the given armature length. 

\section{Challenge 3 - Ease of Use}

While it may be possible to achieve a mechanism that is fast and accurate, it must also be easy to use. For this we are defining "easy to use" as a mechanism that can be assembled with few unique parts, has a wide range of support online/offline and requires few fastener components. Seeing as we cannot model and simulate both mechanism, I will analyze using the available data from similar designs built online.  

The Gantry robot is easy to understand and thus has an overall advantage in this area. Using the RepRap Hydra prototype \ref{fig:Hail_Hydra} Gantry robot we can see that overall it is not a terribly complex design with few fasteners and necessary mounting points \cite{Gantry_Exploded}.  This would make the gantry and ideal candidate for an easy to use system. In addition, since the increase in 3D printing technology, there is a wide range of online support through forums and manuals that will allow for inspiration in the design/build process. 

    \begin{figure}[H]
        \centering
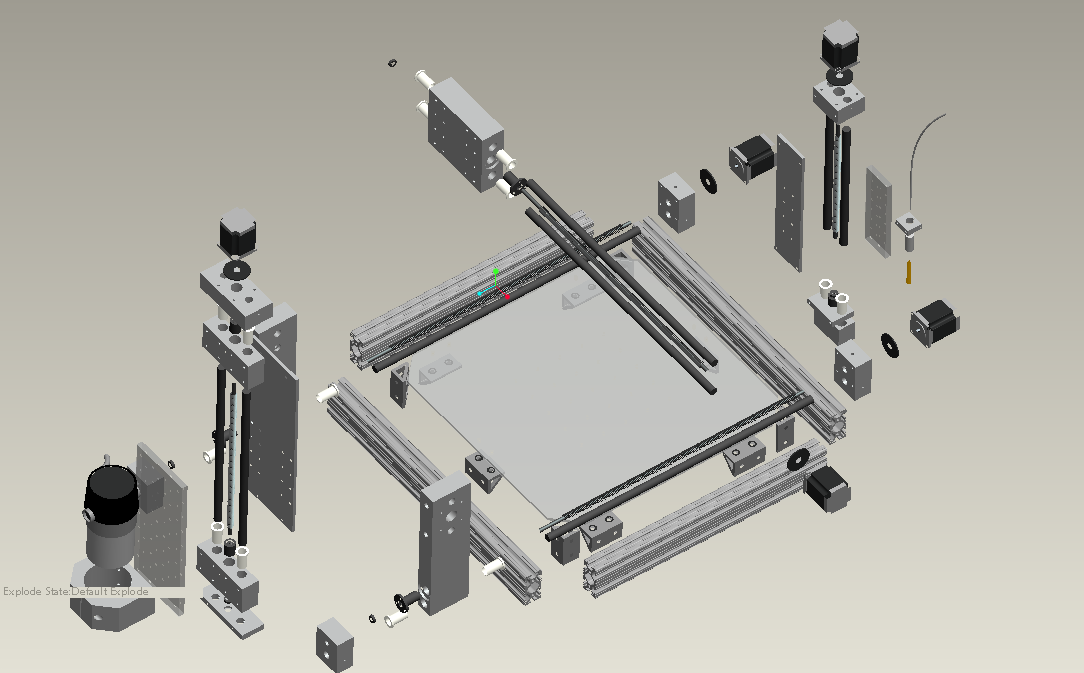
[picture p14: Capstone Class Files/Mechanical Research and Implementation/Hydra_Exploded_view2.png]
        
        \caption{Hydra Gantry Prototype}
        \label{fig:Hail_Hydra}
    \end{figure}
    
The Delta robot has less available online material for possible building structures, save for a few online forums. Based on a custom design it can be seen that the Delta involves a higher level of complexity to it that the Gantry \ref{fig:Delta_Exploded}.

Something to note is that this exploded view only covers 1/3rd of the actual robot mechanism. This was done intentionally to not crowd out the smaller details/components. 

While the delta robot is seen as more complex than the gantry system, it is worth noting that this complexity diminishes as the design progresses. As the system is fleshed out there are only one-time costs towards overall time usage that are spent in comparison to the Gantry robot. For example, once one arm of the Delta robot is decided and designed, this can be copied to the other 3 arms due to the inherent symmetry of the system. The same goes for any other portions of the design related to the linkage design. So while the complexity is increased for designing a Delta robot, this is offset by the fact that these are one-time costs. 

    \begin{figure}[H]
        \centering
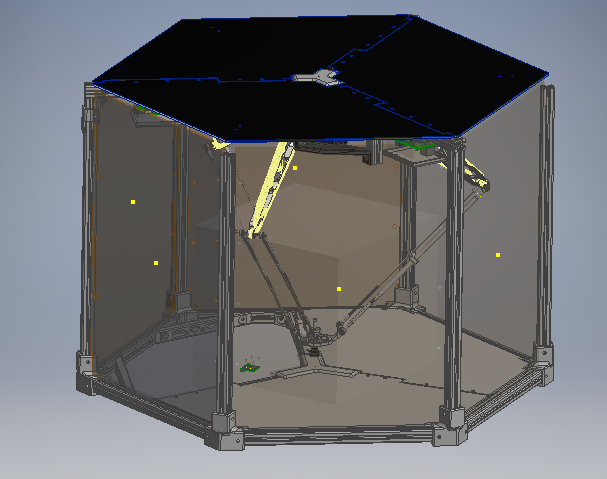
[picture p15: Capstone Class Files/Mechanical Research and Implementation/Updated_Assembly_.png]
        
        \caption{Delta Robot Exploded View}
        \label{fig:Delta_Exploded}
    \end{figure}

\section{Implementation and Discussion}

Being a robotics project there are inherent complexities that must be resolved between subgroups such as the electrical control of the mechanical design, computer commands for electrical control and how effective the mechanical design facilitates the overall process. With that, the project must maintain a high level of communication and simplicity so that all groups are able to understand how their design affects the overall system and others designs \cite{undegrad_robots}.  

Since this system is being designed and manufactured from the ground up, there is the inherent risk that whatever is designed may not work. Working on such a short timeline also means that there will be little time to revise or otherwise improve errors during the build/test phase. This relates back to the complexity component of the chosen mechanical design in which whatever design is chosen must be able to be easily changed or otherwise modified to suit any issues that arise during implementation. 

Between the gantry and delta robot styles they both offer strong benefits in either speed or accuracy. The gantry robot can be considered more precise due to the direct drive system of actuation but is limited to the speed of the drive motors. The delta robot amplifies its drive motor speed by a factor of $cos(\theta)*F_x$ but also amplifies the possible error in movement leading it to lack in accuracy. 

The delta robot seems to be a more attractive offer for this specific application due to its very fast speed and industrial support. The accuracy issues are not extreme and can be improved by the addition of motor encoders which will keep track of possible errors in movement to $\pm 1$ step. The complexity of design can also be simplified through careful effort to create symmetry between the leg/arm units. This design style could also lead to a more efficient design solution even compared to the gantry printer. 

Something to keep in mind is that if the Delta robot fails in the early design stages, there are open source models of gantry robots for CNC or 3D printing applications that could be used as an easy replacement. While lacking in specific benefits towards this project, the gantry is a common and easy design that could be replicated in short order. Using this as a backup solution, this project has a set goal that can be achieved within the allocated time frame. 

\begin{versionhistory}
  \vhEntry{1.0}{12.5.2019}{Jorian Bruslind}{created}
  \vhEntry{1.1}{1.20.2019}{Jorian Bruslind}{Updated final assembly description and profile}
  \vhEntry{1.0}{2.4.2019}{Jorian Bruslind}{Optimized wordings and clarified subjects}
\end{versionhistory}

\bibliographystyle{IEEEtran}
\bibliography{sample}

\end{document}

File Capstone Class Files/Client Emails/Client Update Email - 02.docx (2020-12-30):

Subject: Automated Microbial Analysis Start-Up Packet

Hello Scott,

We have made some good progress towards the overall design of the project. We have partitioned the workload into Mechanical, Electrical and Computer Science sub groups to help with organization.

Mechanical

Mechanically, Jorian has been working on creating a complete modeled design in Autodesk Inventor of the project in order to test out dynamic properties and check for possible physical problems. As of the writing of this email the robot armatures, motor mounts, frame, and homing system have been modeled and assembled with proper constraints. This current design should have full functionality of the delta robot arm and will be able to provide a proof of concept for the dynamics. Based off of these results, we have started ordering preliminary parts such as limit switches, PLA material and 80/20 aluminum struts. With these we hope to provide real life prototypes that we will then optimize. Future developments will be to create a full enclosure for the proposed electronic components and to assemble a loading/unloading system for the PetrFilm.

Electrical

Since the last email, Mack has been working hard to establish rudimentary delta motion. The robot can be controlled by streaming G-Code from the Raspberry Pi, which means the Raspberry Pi can effectively control the position of the motors. However, the system remains in an unpolished state; limit switches and encoder position have not been implemented as of yet, which means the wrong coordinates being sent could potentially cause permanent damage to the system by having the motors rotate too far. Furthermore, the custom PCBs meant to replace the CNC Shield (a component that translates coordinates into motor signals) have been designed and ordered, and should be implemented by next week. Lastly, the vacuum pump system, which will be used to pick up the perti films, has all of the main electrical components ordered, and should have a working proof-of-concept within the week.

Computer Science

The past weeks have been spent finalizing our designs for communication between the RaspberryPi, the brain of our system, the delta robot and the camera. We have also begun the process of researching the best solution for a user interface that will provide you with the appropriate data while still being easy to use. The user interface will start and, if necessary, stop the system and will display an image of the analyzed sample with the microbial count.

In the coming weeks we will continue our initial designs for the system and all of the updates we have provided in this email, as well as any future updates can also be viewed on our GoogleSite. Please do not hesitate to contact us if you have any questions.

Thank you,

Zach Bendt

Jorian Bruslind

Macklin Hall

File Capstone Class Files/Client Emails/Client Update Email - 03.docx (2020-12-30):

Subject: Automated Microbial Analysis Update

Hello Scott,

We have made some good progress towards the overall design of the project. We have partitioned the workload into Mechanical, Electrical and Computer Science sub groups to help with organization.

Mechanical

We have finished ordering the preliminary mechanical components for the project and have started assembly. The entire design has come together fairly well with only a few minor setbacks (usually due to 3D print tolerances). Overall we are looking at a completed design this coming finals week and will be ready to test by winter break. During this time Jorian will be inspecting the design for any revisions that need to be made and possible optimizations.

Electrical

Since the last email, Mack has been working hard to refine the delta motion. The custom PCBs that hold the stepper motor drivers have been designed, ordered, and tested. A 2nd revision, with thermal improvements, as well as readjusted component footprints, has already been designed and ordered. The new design is smaller but more effective than ever. Furthermore, the buck converter for the vacuum pump has been ordered and tested. We found the buck converter to be working as expected. Everything looks very promising for implementation of the vacuum pump to sterilely move our cultural samples from one end of our project to the other. The next step is to design a PCB to hold our relay, which will allow us to turn the vacuum pump on and off via software.

Computer Science

Over the last few weeks most of the time spent on this portion of the project has been centered around increasing the accuracy of the computer vision software and is close to being ready to begin testing of live samples. Zach has also begun researching and experimenting with the design of the graphical user interface. We are also in the process of implementing some of the movement functionality from the Raspberry Pi and hope to have a moving robot by the end of the holiday break.

In the coming weeks we will continue our initial designs for the system and all of the updates we have provided in this email, as well as any future updates can also be viewed on our GoogleSite. We will all be available by email during the holiday break to answer any questions you might have.

Thank you,

Zach Bendt

Jorian Bruslind

Macklin Hall

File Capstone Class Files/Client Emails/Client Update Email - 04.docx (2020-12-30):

Subject: Automated Microbial Analysis Update

Hello Scott,

We have made some good progress towards the overall design of the project. We have partitioned the workload into Mechanical, Electrical and Computer Science sub groups to help with organization.

Mechanical

We’ve noticed some slop overall in the armatures and are working to create a stiffening mechanism to keep this in check. The basic assembly is assembled and ready for testing. So far there’s also been some issues with microstepping the motors and the total torque they produce. This can be resolved by reducing the microstepping but this also reduces the resolution. An acceptable range for us is +- 1mm of tolerance on the end effector and we will keep within this specification.

Going forward we will add in the pneumatic sub system and add mounting structures so that it can be included in the design. We will also be adding a large casing system so that the entire apparatus is enclosed and will not be a hazard.

Electrical

An exciting new development for the electrical branch of this project has been completed! Our stepper motors are now capable of completing a homing sequence, allowing us to know the position of the motors after a power cycle. This is an important stepping stone towards improved reliability and consistent results over time.

Furthermore, I’ve been working with Jorian to develop new PCBs for the stepper motor drivers. We are switching stepper motor drivers to a model with improved robustness and reliability. Additionally, we’ve been developing a new PCB to hold the main ‘brains’ of the project (namely, Arduino Nanos and a Raspberry Pi). These PCBS include much better voltage converters, which should improve system stability and efficiency.

Lastly, we implemented a new power supply that has noticeably better load regulation than the last one we had. This means that the system will not change its behavior under heavy load. Again, this was done in order to increase system robustness and reliability.

Computer Science

Over the last few weeks most of the time spent on this portion of the project has been centered around the design of the user interface as well as getting the coding portion of the control systems. Our goal is to have the basic movements of the bot working in the next week or two. Once we have the basic functionality of the bot is working and we have a test environment built that has stable lighting and camera position we can start fine tuning the computer vision and implement the encoder feedback.

In the coming weeks we will continue our initial designs for the system and all of the updates we have provided in this email, as well as any future updates can also be viewed on our GoogleSite. We will all be available by email during the holiday break to answer any questions you might have.

Thank you,

Zach Bendt

Jorian Bruslind

Macklin Hall

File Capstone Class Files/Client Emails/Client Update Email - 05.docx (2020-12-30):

Subject: Automated Microbial Analysis Update

Hello Scott,

We have made some good progress towards the overall design of the project. We have partitioned the workload into Mechanical, Electrical and Computer Science sub groups to help with organization.

Mechanical

The mechanical design has been updated to reflect some issues that were discovered during the first iteration. We have expanded the T-slot extrusion frame to be much larger so the delta arm can have a much larger work area. We have used around 2x the amount of T-slot, but this is still within the financial parameters. This new design also uses more custom 3D printed mounting blocks which will save on costs for aluminium mounting brackets.

The delta arms have also been updated to use less material by using the generative design function of Autodesk Inventor. Loads were simulated on the original arms and then an optimized design was generated based on those conditions. This new design uses 40% less material overall and will allow for more torque on the end effector (meaning faster movement).

Electrical

Since the last update, the Electrical portion of this project has made steady progress. Despite the delay due to the Coronavirus outbreak in China, we are still on track to complete this project in a timely manner. The custom PCBs Mack and Jorian designed have been completed, fabricated, and shipped to us in the last few days. These PCBs will allow different components in our system to communicate with each other efficiently and effectively. Furthermore, these PCBs will enable a greater degree of motor accuracy, as the newly established encoder signals will only further enhance our error detecting capabilities. Although we still need to assemble and extensively test these PCBs, this still marks a great moment of progress towards our final goal.

Computer Science

Over the last few weeks most of the time spent on this portion of the project has been focused on having the user interface send control signals to the controls processors. We will now begin working on using the feedback from the encoders to allow for the primary processor to have the ability to track and check position of the end effector. This will also include the integration of the kinematics processing that is required because of the delta configuration of the robot. Next week we will also be making an update to the GoogleSite and documentation repository.

In the coming weeks we will continue to integrate our designs into the system. All of the updates we have provided in this email, as well as any future updates can also be viewed on our GoogleSite. As always, we will all be available by email to answer any questions you might have.

Thank you,

Zach Bendt

Jorian Bruslind

Macklin Hall

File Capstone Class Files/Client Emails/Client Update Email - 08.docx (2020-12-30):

Subject: Automated Microbial Analysis Update

Date Sent: 05/07/2020

Hello Scott,

Despite the shutdown of society at large, we have made some good progress towards the overall design of the project. Although physical access to the system has only recently been regained, the time spent since then has not been idly wasted. We have partitioned the workload into Mechanical, Electrical and Computer Science sub groups to help with organization.

Mechanical

The mechanical design is nearing completion and we have added some better joint ends to the lower/upper arms for smoother movement. Currently we are having issues getting the end effector to stay parallel to the surface of the workspace, but expect this to be resolved soon. We will begin working on cleaning up the work space area of wires and other clutter and restraining them to the upper walls of the frame. In addition, we also hope to mount and secure the Raspberry Pi and Central Processor PCB to the inner frame area.

Some improvements that could be made in the next week include perfecting the lower arm lengths so that the end effector is parallel to the floor, adding the suction cup and tube system, and creating secure mounts/coverings for the central processing PCB.

Electrical

The electrical design has not really changed since the last update. The time since has been spent mainly on documentation of the electrical sub-system in one form or another. The GitHub has been updated a great deal, as has the project website. Furthermore, the video covering the details of the entire project has just been completed. This should allow someone to build off of our progress much easier should the opportunity present itself.

Computer Science

The majority of our work on the computer science subsystem over the last few weeks have been centered around documentation. We have prepared presentation materials for the Virtual Expo. This includes a video that describes the entire project and a demonstration of the current functionality of the bot. Moving forward we hope to complete the project over the next few weeks. This will include getting all the controls commands working properly and refining the computer vision to be more accurate.

In the coming weeks we will continue to integrate our designs into the system, as well as update our repositories. All of the updates we have provided in this email, as well as any future updates can also be viewed on our GoogleSite. As always, we will all be available by email to answer any questions you might have.

Thank you for your time,

Zach Bendt

Jorian Bruslind

Macklin Hall

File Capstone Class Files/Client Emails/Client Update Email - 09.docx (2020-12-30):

Subject: Automated Microbial Analysis Update

Date Sent: 05/21/2020

Hello Scott,

Despite the shutdown of society at large, we have made some good progress towards the overall design of the project. Although physical access to the system has only recently been regained, the time spent since then has not been idly wasted. We have partitioned the workload into Mechanical, Electrical and Computer Science sub groups to help with organization.

Mechanical

While working on the assembly we were able to discover some important elements of the ball joint rotation and its mechanical properties. Something that can be improved is the rigidity of the horizontal fastener mount from the upper arm to the lower arm. This improved rigidity solves the issues of an unbalanced end effector that we’ve been experiencing these past few weeks. Apart from that, we have been working to keep the mechanical models and drawings updated and published on the artifact repository webpage (Github).

Electrical

Computer Science

In the coming weeks we will continue to integrate our designs into the system, as well as update our repositories. All of the updates we have provided in this email, as well as any future updates can also be viewed on our GoogleSite. As always, we will all be available by email to answer any questions you might have.

Thank you for your time,

Zach Bendt

Jorian Bruslind

Macklin Hall

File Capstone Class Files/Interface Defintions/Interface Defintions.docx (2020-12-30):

Name | Definition | Properties
rpi_to_csi_camera | *camera connection to RPI | - 8 Megapixel Resolution - MIPI CSI-2 v1.0
120vac_sys | *Wall power to everything | - 120VAC RMS Max - 120VAC RMS Min - 120VAC RMS Nominal - 60 Hz
24v_dc_sys | *24V DC power to motors | - 24VDC Nominal - 6A max (2A per motor)
stepper_driver_phases | *Driver to Motor connection | - 5A max - 2A nominal - 0A min
digital_driver_comms | *Interpreter to motor driver digital lines | - 0V min - 5V max
database_network_to_rpi | *Database to RPI over wifi | - 2.4GHz signal - 10Mb/s bandwidth
rpi_to_display_adapter | *RPI to external monitor | - HDMI mini connector - Standard HDMI video signals
rpi_to_vacuum_activation | *RPI to vacuum pump signal | - 0V min - 5V max
motor_to_encoder_hall_effect | *Magnetic sensor feedback | - 0V min - 5V max
limit_switch_to_rpi | *Limit switches to RPI | - 0V min - 5V max
encoder_to_rpi | *Encoder pulse signals | - 0V min - 5V max

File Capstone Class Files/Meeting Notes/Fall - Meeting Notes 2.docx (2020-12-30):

Automated Microbial Analysis Weekly Meeting Notes

- Group Members in Attendance
  - Bendt, Zachary
  - Bruslind, Jorian
  - Hall, Macklin
- Project Unknowns and Risks
  - Can a single Raspberry Pi be used to do image processing AND motor control?
  - Should we include a depression to catch the finished samples?
  - How can we ensure accurate motor movement?
  - Do we need to implement half-stepping in the motors? If so, will we still have enough torque?
  - What purpose does our final project aim to fulfill?
- Tasks from This Week
  - Zach
    - Drafted v.1 Block diagram for data collection (1 hr)
    - Engineering Requirements Draft(2 hrs)
    - Drafted Client Email update (1hr)
  - Jorian
    - Added model for limit switch system(1hr)
    - Drafted mounting system for arm linkages(2hrs)
    - Drafted motor mounts (2hrs)
    - Purchased motors (15min)
  - Mack
    - Installed Python and began to learn Python syntax (1 hr)
    - Rewrote PowerShell script in Python (30 min)
    - Troubleshot Python script (1 hr)
    - Researched and purchased IEC320 C14 socket for project (15 min.)
- Group Meeting Topics
  - Raspberry Pi and Arduino interactions
  - Pertinent coding languages and libraries
  - Hardware interaction with code structure
  - Group roles and responsibilities
  - Custom PCB implementations and features
  - Power delivery methods
  - Meeting scheduling
  - Asana task tracking
- New Items
  - Determined Raspberry Pi will be sending G-Code to Arduino via a Python 3.x script
  - Determined that code will resemble a linear state-machine
  - Scheduled Scope and Requirements Meeting for Oct. 23rd at 11:40
  - Delegated administrative tasks to individual group members on Asana
- Tasks for Next Week
  - Zach
    - Finalize Client Update Email
    - Scope and Requirements Meeting Prep
  - Jorian
    - Assemble mechanical design for verification/review (5hrs)
    - Create RPI mounting system (2hrs)
  - Mack
    - Assemble and calibrate motor power delivery system (1.5 hrs)
    - Validate motor drive system (1.5 hrs)
  - Everyone
    - Keep an eye on Asana page for task updates
- Hours This Week

| Total Hours | Hours w/ Team | Hours Helping
Bendt, Zachary | 3.25 | 1.25 | 1.25
Bruslind, Jorian | 5.25 | 3 | 1
Hall, Macklin | 4 | 1.25 | 1.25

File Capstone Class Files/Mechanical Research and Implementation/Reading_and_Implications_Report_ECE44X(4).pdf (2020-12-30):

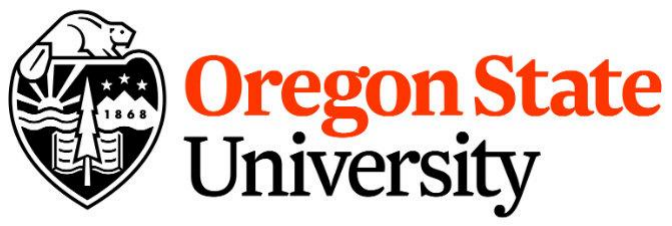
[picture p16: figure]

ECE 44x - Group 3

Automated Microbial Analysis

# Reading and Implications Report

Mechanical Design - Connectors and Enclosures

## Jorian Bruslind

April 10, 2020

## Contents

1 Introduction | 2
2 Summary of Expert Topic Areas and Design Challenges | 3
3 Challenge 1 - Accuracy | 4
4 Challenge 2 - Speed | 6
5 Challenge 3 - Ease of Use | 7
6 Implementation and Discussion | 8

1

Mechanical Design | Automated Microbial Analysis

## Abstract

The purpose of this document is to provide context for the reader behind the design choices made within the perview of the mechanical design aspect of the Automated Microbial Analysis capstone project. This project aims to manipulate, analyze, and physically sort microbial samples present on 3M Petrifilm. This document will cover the mechanical concepts present in the system, the design choices for each concept and the proposed solution for each choice. Finally, this document will then cover the expected challenges with this project and possible solutions to said challenges.

## 1 Introduction

The Automated Microbial Analysis project aims to develop a system which is able to analyze a series of microbial samples on a special media called PetriFilm [1] automatically. This is a 3M product that is used in a variety of scientific capacities, mainly in food science and the medical field.


Figure 1: 3M PetriFilm Single Sample

PetriFilm is a very thin paper-like substance which has 2 layers: on one there is an agar media film that is used to grow bacterium, On the other there is a wax coating that is used to seal the sample from outside interference. A liquid sample can be applied to this agar film and left to incubate over a period of 1 - 2 days. After this time, the bacteria that were present within the sample will have had enough time to grow into colonies which are visible to the human eye. These colonies can be counted and the original number of bacterium per unit volume can be known from the original sample. The process to count the bacteria samples and categorize them into datasets is often tedious and can take a human operator around 1 - 2 minutes per sample [2]. With sample sizes of 50 - 60, this process can easily take over an hour. The goal of our project is to use an automated system to count these bacteria colonies in sample sets of upwards of 100+ in as little as 20 minutes. This data will be automatically stored and tabulated within the client’s original database.

For this process it is necessary to create a physical manipulation system that will be able to move paper-like objects in an efficient and precise manner. These samples are somewhat delicate and require careful handling. In addition, they must be placed in a specific orientation so that the bacterial samples can be easily read by some visual component. Therefore it is necessary to create a mechanical system that can be easily made precise and is able to be used for our intended implementation. In addition, there will be designated areas for loading/unloading of samples so that the overall process requires as little human intervention as possible.

Once the loaded, the system will take over and begin the counting process for each sample. There will be error correction and state information for each portion of the counting cycle to ensure the samples are not damaged and to reduce the chance of a miscount. After the sample has been counted and cataloged, it will be placed into one of two sections designated "Pass" or "Needs Review" where they can be sorted by a human operator.

This document aims to provide context for my responsibilities as they apply to the project and what steps were taken to achieve the goals outlined above. I have personally been involved in a variety of robotics related projects working with groups ranging from 1 - 20 people. I have had experience working with control systems, mechanical design, and automated systems and it is my hope that I can apply that experience towards the success of this project.

## 2 Summary of Expert Topic Areas and Design Challenges

This project requires a great deal of mechanical, electrical and computer science engineering and necessitates the complexity of having each area work together. To help simplify the design process, each team member is assigned an area of expertise that they are responsible for. For me specifically, I will be responsible for the mechanical design and hardware implementation of our system.

### 2.1 Area of Expertise

For this project, 2 mechanical systems came to mind that are used in similar applications. The first being a printer while the second was a pick and place machine. Both use fairly intricate mechanical systems to preform their function and as such I need to be aware of their abilities and limitations. It is important to consider parameters such as speed, simplicity in design, cost, and ease of use when designing a system such as ours and it will be my responsibility to analyze each when considering the different options.

For this area of expertise, I will need to be responsible for the design and simulation of our mechanical system. To do so I will use Computer Assisted Design (CAD) in the form of Autodesk Inventor to model our entire system before assembly. I have had around 6 years experience working with Inventor in other applications and feel confident in it’s ability for CAD modeling.

### 2.2 Design Challenges

The project requirements that most relate to my area of expertise include: Accuracy, Sample Preservation, Fast, Enclosed Work Area, and Ease of Use. All of these requirements require the mechanical system in some way, shape or form. With this in mind my research focused on the possible mechanical systems and their ability to meet the aforementioned requirements. Speed and accuracy were the two requirements I spend the most amount of focus on as they were ultimately the most influential in deciding which mechanism to go with. In addition, most all systems can be designed in such a way to be easy to use, have an enclosed work area, and prioritizing accuracy provides a means for sample preservation.

A focus of my research was what mechanical systems were used in industry for similar purposes to ours. The point being that many companies would have invested time and money into figuring out the most efficient way to preform their specific task. First, an analysis of the task that is to be preformed indicated 2 possible mechanisms: Pick and Placing and printing/scanning. The PetriFilm can be thought of as slips of paper in the fact that they are both light and thin. Therefore, the most common forms of industrial robotics that deal with paper-like objects are through printing/scanning mechanisms and pick/placing mechanisms [3]. The printing/scanning methods (as seen in 2b)seem to be the most ideal, considering the act of imaging paper is the same process that we must do to the PetriFilm. Within the pick and placing category, the most popular type of robots found in industry include the Delta robot configuration 2a and the Cartesian (Gantry) robot configuration 2c. For simplicity, I will focus on the contrasts between our 3 stated requirements and the aforementioned robotic systems.


(a) Modeled Delta Robot)


(b) Simple Printer Schematic)


(c) Modeled Gantry Robot

## 3 Challenge 1 - Accuracy

Arguably, the most important aspect of our project is that is must be accurate so as not to damage the provided samples and to improve it’s overall time cost for this process (less mistakes mean less time needed to recover). To measure accuracy, I investigated 2 components of the mechanical systems, the end effector accuracy and what steps are necessary to improve the end effector accuracy. The end effector in this case is whatever part is going to be moving the samples during the process. It is necessary to also investigate possible improvements to the accuracy of the systems as some systems may not have the best inherent stability, but for relatively little cost they could be improved. For simplicity, I am assuming all motors used are NEMA 17 200 step/rev 2 phase stepper motors [4] so as to standardize the investigation.

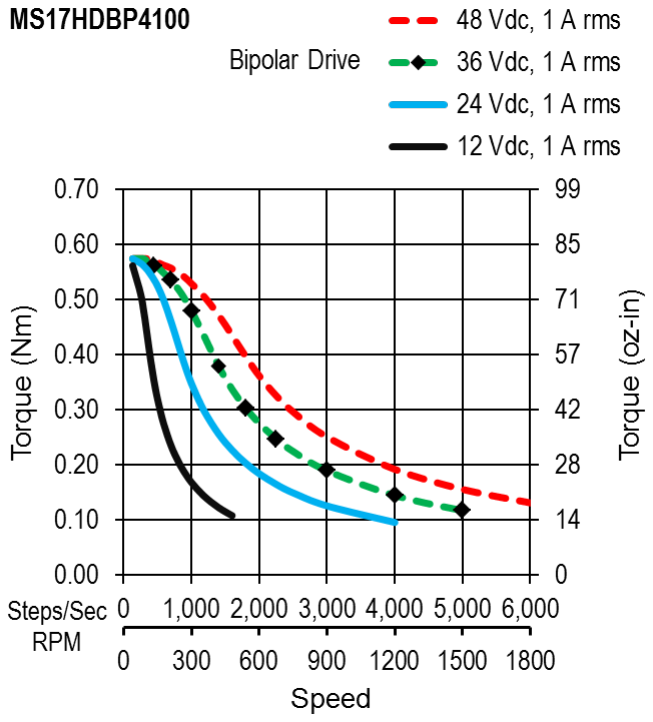
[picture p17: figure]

(a) NEMA 17 Stepper Motor | (b) NEMA 17 Torque Curve [5]

If we were to model our design after a printer/scanner then it would be accurate to within a few mm, however it comes at the cost of many different sensors and a complex mechanical system. Looking at the overall design of a printer system, it can be seen that in order to facilitate the processing of samples in a stack, there must be mechanisms that keep the stack in order, in place, and restricted enough so that only 1 sample is taken at one time. It is known that printers will often experience jams or other physical problems that would ultimately destroy the samples if they occurred. So while it may be possible to achieve accuracy to a fine degree, the amount of extra work required to achieve this is beyond the scope of our ability.

Other possible options for this design would be to employ a robotic system to manipulate samples within a set workspace. Both Gantry and Delta robots are renown for their ability or preform pick and place operations accurately. The reason for choosing pick and place for our operation is that samples can easily be put into a stack and picked off / placed down for analysis.

Of the two options, the easiest to understand is probably the Cartesian (Gantry) robot. This mechanical system is simple in that it just uses 1 stepper to move in each Cartesian direction. Therefore the accuracy of the overall system is just limited by the accuracy of the chosen stepper motor. Depending on the operation, it may be necessary to scale the torque of the stepper motor through gear/pulley ratios which would ultimately reduce the overall accuracy [6], but for the purposes of this document we will assume there is no reduction.


Figure 4: Possible gear reduction using pulley

The Delta robot is a little more complicated in the analysis of accuracy. Similar to the Gantry robot, the accuracy is directly related to the chosen stepper motors, however the error factor is multiplied by a factor related to the delta robot armature length. This is due in fact to the idea that the stepper will drive a longer arm which in turns moves the end effector. Therefore a small error on part of the rotation of the stepper, will induce a larger error (translationally) at the end of the arm length (arc length vs angle). Therefore the Delta robot will have a similar accuracy to the Gantry robot just scaled by a factor of the chosen armature length.


(a) Gantry work area


(b) Delta work area from simulation [7]

## 4 Challenge 2 - Speed

Speed is also an important consideration for this project. while accuracy ensures the samples will not be damaged, speed is ultimately speed is why the project exists at all. In order to consider the project effective, it must be able to move samples on the order of 100 / 5 - 10 min. With this in mind, I thought of speed as very close (but not quite as) important as accuracy.

For the Gantry robot, speed is limited to the abilities of the chosen stepper motors and the location of the sample input/output stacks [8]. This can be amplified through the use of gearboxes or pulley systems, with the cost of losing some torque or overall force power.

The Delta robot is a little more complicated. The speed that this mechanism can achieve is mostly based off of its armature length as explained above. For every 1

- of rotation, the actual movement is based off the arc length which is in turn based off the length of the armature. By deriving the Delta robot’s forward kinematic equations (where, given (Θ1, Θ2, Θ3) we can determine (X0, Y0, Z0)), it is possible to determine by what factor the actual speed is increased. Using the model variables found in 6a the derivation follows between images [9].


(a) Labeled Delta Variables


(b) Defining Delta parameters with corresponding equations


Figure 7: Forward Kinematics calculations

Generalizing from 7 we can determine that the rotation of all 3 motors 1

- would increase the Z
axis parameter by a factor of cos(θ) · Fx where Fx is the given armature length.

## 5 Challenge 3 - Ease of Use

While it may be possible to achieve a mechanism that is fast and accurate, it must also be easy to use. For this we are defining "easy to use" as a mechanism that can be assembled with few unique parts, has a wide range of support online/offline and requires few fastener components. Seeing as we cannot model and simulate both mechanism, I will analyze using the available data from similar designs built online.

The Gantry robot is easy to understand and thus has an overall advantage in this area. Using the RepRap Hydra prototype 8 Gantry robot we can see that overall it is not a terribly complex design with few fasteners and necessary mounting points [10]. This would make the gantry and ideal candidate for an easy to use system. In addition, since the increase in 3D printing technology, there is a wide range of online support through forums and manuals that will allow for inspiration in the design/build process.


Figure 8: Hydra Gantry Prototype

The Delta robot has less available online material for possible building structures, save for a few online forums. Based on a custom design it can be seen that the Delta involves a higher level of complexity to it that the Gantry 9.

Something to note is that this exploded view only covers 1/3rd of the actual robot mechanism. This was done intentionally to not crowd out the smaller details/components.

While the delta robot is seen as more complex than the gantry system, it is worth noting that this complexity diminishes as the design progresses. As the system is fleshed out there are only one-time costs towards overall time usage that are spent in comparison to the Gantry robot. For example, once one arm of the Delta robot is decided and designed, this can be copied to the other 3 arms due to the inherent symmetry of the system. The same goes for any other portions of the design related to the linkage design. So while the complexity is increased for designing a Delta robot, this is offset by the fact that these are one-time costs.

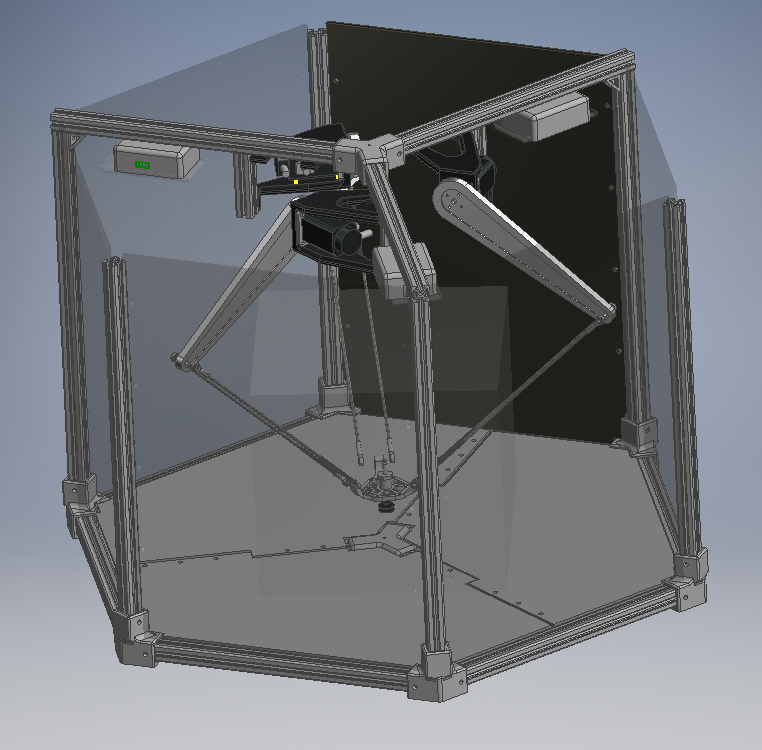
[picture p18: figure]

Figure 9: Delta Robot Exploded View

## 6 Implementation and Discussion

Being a robotics project there are inherent complexities that must be resolved between subgroups such as the electrical control of the mechanical design, computer commands for electrical control and how effective the mechanical design facilitates the overall process. With that, the project must maintain a high level of communication and simplicity so that all groups are able to understand how their design affects the overall system and others designs [11].

Since this system is being designed and manufactured from the ground up, there is the inherent risk that whatever is designed may not work. Working on such a short timeline also means that there will be little time to revise or otherwise improve errors during the build/test phase. This relates back to the complexity component of the chosen mechanical design in which whatever design is chosen must be able to be easily changed or otherwise modified to suit any issues that arise during implementation.

Between the gantry and delta robot styles they both offer strong benefits in either speed or accuracy. The gantry robot can be considered more precise due to the direct drive system of actuation but is limited to the speed of the drive motors. The delta robot amplifies its drive motor speed by a factor of cos(θ) ∗ Fx but also amplifies the possible error in movement leading it to lack in accuracy.

The delta robot seems to be a more attractive offer for this specific application due to its very fast speed and industrial support. The accuracy issues are not extreme and can be improved by the addition of motor encoders which will keep track of possible errors in movement to ±1 step. The complexity of design can also be simplified through careful effort to create symmetry between the leg/arm units. This design style could also lead to a more efficient design solution even compared to the gantry printer.

Something to keep in mind is that if the Delta robot fails in the early design stages, there are open source models of gantry robots for CNC or 3D printing applications that could be used as an easy replacement. While lacking in specific benefits towards this project, the gantry is a common and easy design that could be replicated in short order. Using this as a backup solution, this project has a set goal that can be achieved within the allocated time frame.

## Revision History

Revision | Date | Author(s) | Description
1.0 | 12.5.2019 | Jorian Bruslind | created
1.1 | 1.20.2019 | Jorian Bruslind | Updated final assembly description and profile
1.0 | 2.4.2019 | Jorian Bruslind | Optimized wordings and clarified subjects

## References

[1] beveragedaily. | com, | “Food | safety | is | increasing | in | China | and | India,” | bever-
agedaily.com, May 2014. [Online]. Available: | https://www.beveragedaily.com/Article/2014/
05/26/3M-s-Petrifilm-30th-anniversary (https://www.beveragedaily.com/Article/2014/05/26/3M-s-Petrifilm-30th-anniversary)
[2] “3MTM | Petrifilm | Plates: | Microbial | Food | Testing, | Quality | Indicator | Test | | 3M
United | States,” | Dec | 2019, | [Online; | accessed | 5. | Dec. | 2019]. | [Online]. | Avail-
able: | https://www.3m.com/3M/en_US/company-us/all-3m-products/~/All-3M-Products/
Food-Safety-Microbiology/Quality-Indicator-Testing-3M-Petrifilm-Plates/?N=5002385+ 8711017+8711414+8716589+3294857497&rt=r3#howtouse (https://www.3m.com/3M/en_US/company-us/all-3m-products/~/All-3M-Products/Food-Safety-Microbiology/Quality-Indicator-Testing-3M-Petrifilm-Plates/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)
[3] “Types of Robots Based on Configuration | Plant Automation Technology,” May 2018, [Online;
accessed 5. Dec. 2019]. [Online]. Available: https://www.plantautomation-technology.com/articles/types-of-robots-based-on-configuration (https://www.plantautomation-technology.com/articles/types-of-robots-based-on-configuration)
[4] Nema, “Motion/Position Control Motors, Controls and Feedback Devices,” Dec 2019, [Online; accessed 5. Dec. 2019]. [Online]. Available: https://www.nema.org/Standards/Pages/Motion-Position-Control-Motors-Controls-and-Feedback-Devices.aspx (https://www.nema.org/Standards/Pages/Motion-Position-Control-Motors-Controls-and-Feedback-Devices.aspx)
[5] “NEMA | 17 | Standard | Hybrid | Stepper | Motors,” | Dec | 2019, | [Online; | ac-
cessed | 5. | Dec. | 2019]. | [Online]. | Available: | https://www.moonsindustries.com/series/
nema-17-standard-hybrid-stepper-motors-b020105 (https://www.moonsindustries.com/series/nema-17-standard-hybrid-stepper-motors-b020105)
[6] “Carlicia Layosa,” | Dec 2019, | [Online; | accessed 5. Dec. 2019]. [Online]. Available:
https://blog.misumiusa.com/sizing-timing-belts-and-pulleys
[7] “SourceForge,” Dec 2019, [Online; accessed 5. Dec. 2019]. [Online]. Available: https: //sourceforge.net/projects/visual-delta3
[8] M. McTaggart, R. Smith, J. Erskine, R. Grinover, and C. Lehnert, “Mechanical Design of a Cartesian Manipulator for Warehouse Pick and Place,” ResearchGate, Sep 2017. [Online]. Available: https://www.researchgate.net/publication/319876160_Mechanical_Design_of_a_Cartesian_Manipulator_for_Warehouse_Pick_and_Place (https://www.researchgate.net/publication/319876160_Mechanical_Design_of_a_Cartesian_Manipulator_for_Warehouse_Pick_and_Place)
[9] “Delta robot kinematics - Tutorials,” Dec 2019, [Online; accessed 5. Dec. 2019]. [Online]. Available: http://forums.trossenrobotics.com/tutorials/introduction-129/delta-robot-kinematics-3276
[10] “Hydra-MMM Prototype - RepRap,” Dec 2018, [Online; accessed 5. Dec. 2019]. [Online]. Available: https://reprap.org/wiki/Hydra-MMM_Prototype
[11] D. Blank, D. Kumar, J. Marshall, and L. Meeden, “Advanced robotics projects for undergraduate students.” 01 2007, pp. 10–15.

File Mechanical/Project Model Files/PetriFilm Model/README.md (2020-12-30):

#	PetriFilm model

Unfortunately we didn't have a 3D model of Petrifilm available to use for our system. So this directory contains our custom model we designed/used to reference our measurements off of. This was made using the Anaerobic film samples donated by Analysis Laboratories.



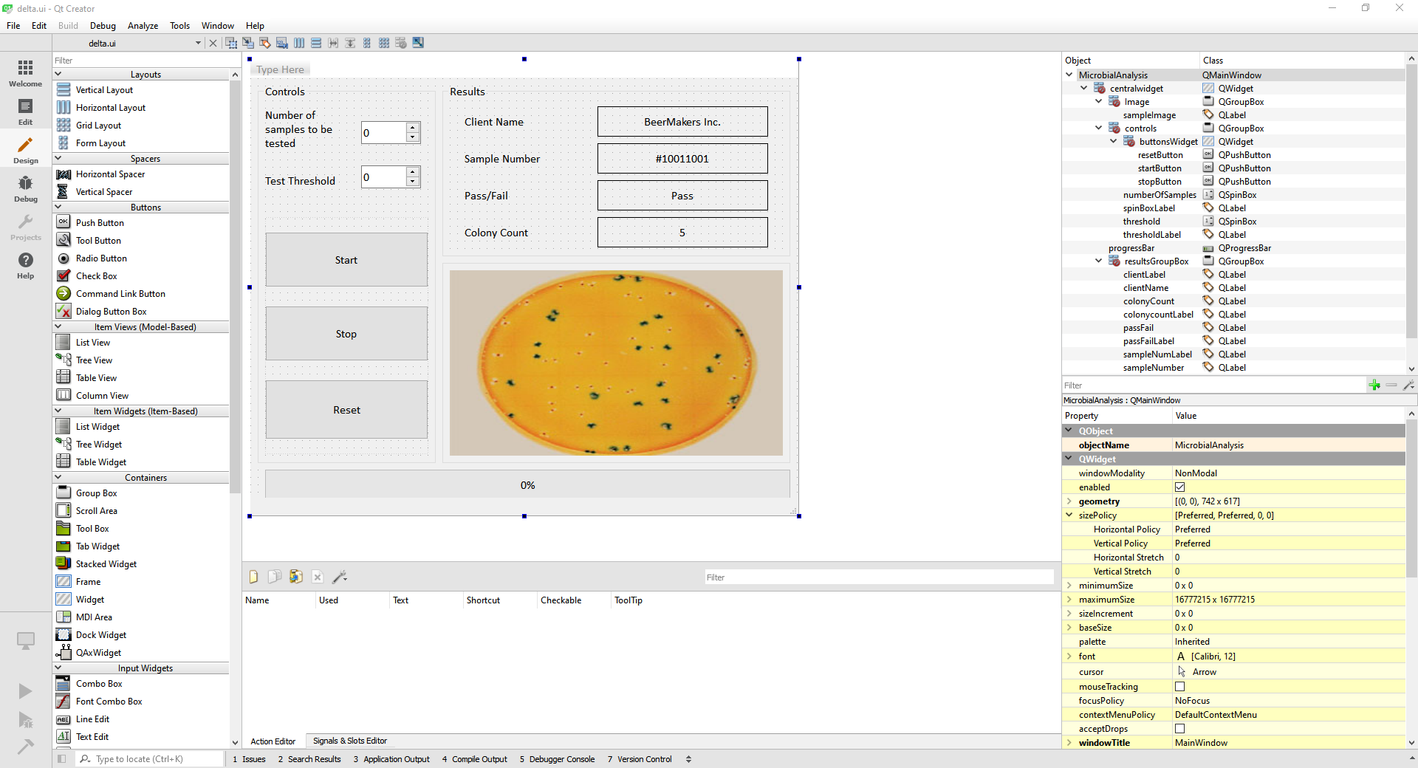
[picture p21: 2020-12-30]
Computer Science/Images/Qt_Designer.png

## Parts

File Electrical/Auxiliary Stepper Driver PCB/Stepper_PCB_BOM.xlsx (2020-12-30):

Stepper Driver PCB |  |  | Engineer: | Jorian Bruslind |  | Prepared For: | Automated Microbial Analysis Capstone |  | Sheet ID | 1NSlFSz8Fo2ZRfzD6EsASZnQmnRLNQRVN0NdUrKfXu1c |  |  |  | Manuf. Capability | 0 | To Manufacture | 3
Cat | Item Name | Part Designator (if applicable) | Part Value | Link | Vendor | Vender No | Price | BOM Quantity | BOM Total | Purch. Quan. | Notes | BOM Total: | $25.71 | Purchase Total: | $77.13
Cap | CAP CER 2200PF 50V X7R 0805 | C7 | 2200pF | link (https://www.digikey.com/product-detail/en/samsung-electro-mechanics/CL32B225KCJSNNE/1276-3362-1-ND/3891448) | DigiKey | 399-1151-1-ND | 0.1 | 1 | 0.1 | 3 |  | $0.30
Cap | CAP CER 10000PF 50V X7R 0603 | C3, C4, C6, C9 | .1uF | link (https://www.digikey.com/product-detail/en/taiyo-yuden/UMK325BJ106MM-P/587-5962-1-ND/7675082) | DigiKey | 399-7842-1-ND | 0.1 | 4 | 0.4 | 12 |  | $1.20
Res | RES 0.12 OHM 5% 1/10W 0603 | R4, R5 | .12 Ohm | link (https://www.digikey.com/product-detail/en/on-semiconductor/NSR20F30NXT5G/NSR20F30NXT5GOSCT-ND/2409706) | DigiKey | P.12AHCT-ND | 0.27 | 2 | 0.54 | 6 |  | $1.62
Res | RES SMD 1K OHM 5% 1/10W 0603 | R2 | 1K Ohm | link (https://www.digikey.com/product-detail/en/vicor-corporation/PI3546-00-LGIZ/1102-5475-ND/5321312) | DigiKey | 311-1.0KGRCT-ND | 0.1 | 1 | 0.1 | 3 |  | $0.30
Res | RES 1.1 OHM 1% 1/8W 0603 | R1 | 1.1 Ohm | link (https://www.digikey.com/product-detail/en/eaton-electronics-division/HCV1206-R90-R/283-4586-1-ND/5418752) | DigiKey | 2019-RK73H1JTTD1R10FCT-ND | 0.1 | 1 | 0.1 | 3 |  | $0.30
Res | CAP CER 2.2UF 50V X5R 0603 | C8 | 2.2uF | link (https://www.digikey.com/product-detail/en/stackpole-electronics-inc/RMCF1210JT1K00/RMCF1210JT1K00CT-ND/1942858) | DigiKey | 490-10733-1-ND | 0.33 | 1 | 0.33 | 3 |  | $0.99
Cap | CAP CER 10UF 50V X5R 1210 | C1, C2, C10, C11, C12 | 10uF | link (https://www.digikey.com/product-detail/en/panasonic-electronic-components/ERJ-14YJ113U/P11KVCT-ND/249617) | DigiKey | 587-5962-1-ND | 0.65 | 5 | 3.25 | 15 |  | $9.75
Res | RES SMD 100K OHM 0.5% 1/16W 0603 | R3 | 100K Ohm |  | DigiKey | RR08P100KDCT-ND | 0.1 | 1 | 0.1 | 3 |  | $0.30
Con | TERM BLOCK HDR 4POS 90DEG 3.81MM | J2 | Con |  | DigiKey | 277-1208-ND | 1.71 | 1 | 1.71 | 3 |  | $5.13
Con | CONN HDR 8POS 0.1 TIN PCB | J8-L, J8-R | Con |  | DigiKey | S7006-ND | 0.65 | 2 | 1.3 | 6 |  | $3.90
Res | RES SMD 330 OHM 1% 1/5W 0603 | R6, R7, R8 | 330 Ohm |  | DigiKey | A129541CT-ND | 0.1 | 3 | 0.3 | 9 |  | $0.90
IC | IC MTR DRV 4.75-28V QFN28 | U1 | IC |  | DigiKey | 1460-1398-1-ND | 2.74 | 1 | 2.74 | 3 |  | $8.22
Con | CONN HEADER VERT 2POS 2.54MM | J5, J6, J7, J9 | Con |  | DigiKey | 732-5315-ND | 0.13 | 4 | 0.52 | 12 |  | $1.56
Con | HIGH QUALITY GOLD PLATED XT30 MA | J4 | Con |  | DigiKey | 1738-1436-ND | 1.92 | 1 | 1.92 | 3 |  | $5.76
Res | RES SMD 1.6K OHM 0.5% 1/16W 0603 | R9 | 1.6K Ohm |  | DigiKey | RR08P1.6KDCT-ND | 0.11 | 1 | 0.11 | 3 |  | $0.33
Con | CONN MOD JACK 8P8C R/A UNSHLD | J1 | Con |  | DigiKey | RJHSE-5080-ND | 0.78 | 1 | 0.78 | 3 |  | $2.34
Con | CONN D-SUB RCPT 9POS R/A SOLDER | J3 | Con |  | DigiKey | A32117-ND | 3.74 | 1 | 3.74 | 3 |  | $11.22
IC | DC DC CONVERTER 5V | X1 | IC |  | DigiKey | 296-49462-1-ND | 5.95 | 1 | 5.95 | 3 |  | $17.85
LED | LED RED CLEAR 0603 SMD | D1, D2 | LED |  | DigiKey | 732-4978-1-ND | 0.14 | 1 | 0.14 | 3 |  | $0.42
LED | LED GREEN CLEAR 0603 SMD | D3, D4 | LED |  | DigiKey | 732-4980-1-ND | 0.14 | 2 | 0.28 | 6 |  | $0.84
Cap | CAP CER 1UF 10V X5R 0603 | C5 | 1uF |  | DigiKey | 1276-1182-1-ND | 0.1 | 1 | 0.1 | 3 |  | $0.30
IC | IC MCU 8BIT 8KB FLASH 8DIP | U2 | IC |  | DigiKey | ATTINY85-20PU-ND | 1.2 | 1 | 1.2 | 3 |  | $3.60

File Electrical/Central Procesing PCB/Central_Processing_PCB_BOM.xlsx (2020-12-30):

Circuitmaker Project Name |  |  | Engineer: | M. Hall, J. Bruslind, Z. Bendt |  | Prepared For: | Automated Microbial Analysis Capstone |  | Sheet ID | 1v8RpDhfu9nJetK7O2sICyVqOKlSaCVFZ8NGJmMl5BQc |  |  |  | Manuf. Capability | 0
Cat | Item Name | Part Designator (if applicable) | Part Value | Link | Vendor | Vender No | Price | BOM Quantity | BOM Total | Purch. Quan. | Notes | BOM Total: | $49.88 | Purchase Total: | $99.76
5V Regulator | Texas Instruments UA78M05IDCYR | Q1,Q2 | 5V @ 0.5A | link (https://www.digikey.com/product-detail/en/texas-instruments/UA78M05IDCYR/296-17616-1-ND/706597) | DigiKey | 296-17616-1-ND | 0.61 | 2 | 1.22 | 4 |  | $2.44
XT30 | DFRobot FIT0586 | J0 | 2-Pin Con. | link (https://www.digikey.com/products/en?keywords=DFRobot%20FIT0586) | DigiKey | 1738-1436-ND | 1.92 | 1 | 1.92 | 2 | Might not need to purchase | $3.84
USB Mini Con. | USB Mini UJ2-MBH-1-SMT-TR | J1,J2 | USB Mini | link (https://www.digikey.com/product-detail/en/cui-devices/UJ2-MBH-1-SMT-TR/102-4003-1-ND/6187925) | DigiKey | 102-4003-1-ND | 0.54 | 2 | 1.08 | 4 |  | $2.16 |  | $95.56
Ethernet Port | Amphenol ICC RJHSE5080 | J3,J4,J5 | RJ45 | link (https://www.digikey.com/product-detail/en/amphenol-icc-commercial-products/RJHSE-5080/RJHSE-5080-ND/1242687) | DigiKey | RJHSE-5080-ND | 0.78 | 3 | 2.34 | 6 |  | $4.68
3x2 Headers | TE Connectivity 826632-3 | P1,P2 | 3x2 Male | link (https://www.digikey.com/product-detail/en/te-connectivity-amp-connectors/826632-3/A114547-ND/2276139) | DigiKey | A114547-ND | 0.87 | 2 | 1.74 | 4 |  | $3.48
6-Pin JST | JST B6B-PH-K-S(LF)(SN) | P3 | 6x1 Male | link (https://www.digikey.com/products/en?keywords=JST%20B6B-PH-K-S(LF)(SN)) | DigiKey | 455-1708-ND | 0.33 | 1 | 0.33 | 2 |  | $0.66
Fan Header | TE Connectivity 640456-3 | P4,P5,P6,P9,P10 | 3x1 Male | link (https://www.digikey.com/product-detail/en/640456-3/A19470-ND/259010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) | DigiKey | A19470-ND | 0.14 | 5 | 0.7 | 10 |  | $1.40
UART Chip | FT232RL-Reel | U3,U4 | 5V | link (https://www.digikey.com/product-detail/en/ftdi-future-technology-devices-international-ltd/FT232RL-REEL/768-1007-1-ND/1836402) | DigiKey | 768-1007-1-ND | 4.5 | 2 | 9 | 4 |  | $18.00
12V Regulator | Cyntec MUN24AD03-SM | U1 | 12V | link (https://www.digikey.com/product-detail/en/delta-electronics-cyntec/MUN24AD03-SM/2037-MUN24AD03-SMCT-ND/9839047) | DigiKey | 2037-MUN24AD03-SMCT-ND | 3.92 | 1 | 3.92 | 2 |  | $7.84
5V Regulator | SRBH-06H1A1G | U6 | 6A @ 5V | link (https://www.digikey.com/product-detail/en/bel-power-solutions/SRBH-06H1A1G/179-SRBH-06H1A1G-ND/8556188) | DigiKey | 179-SRBH-06H1A1G-ND | 8.97 | 1 | 8.97 | 2 |  | $17.94
RPi Headers | TE Connectivity 4-1734506-3 | U7 | 20x2 Female | link (https://www.digikey.com/product-detail/en/0ZCH0200FF2E/507-1792-1-ND/4156310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) | DigiKey | A115198-ND | 1.86 | 1 | 1.86 | 2 |  | $3.72
uC | ATMEGA328PB-AU | STEPPER_,AUX_ | 5V | link (https://www.digikey.com/product-detail/en/microchip-technology/ATMEGA328PB-AU/ATMEGA328PB-AU-ND/5638812) | DigiKey | ATMEGA328PB-AU-ND | 1.34 | 2 | 2.68 | 4 |  | $5.36
uC Sockets | Preci-Dip 310-87-115-41-001101 | Stepper_Arduino,AUX_Arduino | 15x1 Female | link (https://www.digikey.com/product-detail/en/preci-dip/310-87-115-41-001101/1212-1103-ND/3757353) | DigiKey | 1212-1103-ND | 0.94 | 4 | 3.76 | 8 |  | $7.52
Relay | Kemet EC2-5NU | K1,K2 | 5V | link (https://www.digikey.com/products/en?keywords=Kemet%20EC2-5NU) | DigiKey | 399-11052-5-ND | 1.63 | 2 | 3.26 | 4 |  | $6.52
Schottky Diode | MBR0520LT1G | VD1,VD2 | 20V @ 0.5A | link (https://www.digikey.com/product-detail/en/on-semiconductor/MBR0520LT1G/MBR0520LT1GOSCT-ND/917965) | DigiKey | MBR0520LT1GOSCT-ND | 0.3 | 2 | 0.6 | 4 |  | $1.20
Resonator | AS-16.000-18 | X1,X2 | 16MHz | link (https://www.digikey.com/product-detail/en/AS-16.000-18/2151-AS-16.000-18-ND/10271769/?itemSeq=317177599) | DigiKey | 2151-AS-16.000-18-ND | 0.66 | 2 | 1.32 | 4 |  | $2.64
Push Button | TE Connectivity 2-1437565-9 | S1,S2 | 0.05A @ 24V | link (https://www.digikey.com/product-detail/en/te-connectivity-alcoswitch-switches/1825910-6/450-1650-ND/1632536) | DigiKey | 450-1650-ND | 0.1 | 2 | 0.2 | 4 |  | $0.40
Capacitor | Samsung CL10A475KP8NNNC | C1,C3,C6,C8 | 4.7uF | link (https://www.digikey.com/product-detail/en/CL10A475KP8NNNC/1276-1044-1-ND/3889130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) | DigiKey | 1276-1044-1-ND | 0.13 | 4 | 0.52 | 8 |  | $1.04
Capacitor | Kemet C0603C104Z3VACTU | C2,C4,C5,C7,C9,C10 | 0.1uF | link (https://www.digikey.com/product-detail/en/kemet/C0603C104Z3VACTU/399-1100-1-ND/411375) | DigiKey | 399-1100-1-ND | 0.1 | 6 | 0.6 | 12 |  | $1.20
Capacitor | Samsung CL31A106MBHNNNE | C11,C12,C13,C14 | 10uF | link (https://www.digikey.com/product-detail/en/samsung-electro-mechanics/CL31A106MBHNNNE/1276-6736-1-ND/5961595) | DigiKey | 1276-6736-1-ND | 0.34 | 4 | 1.36 | 8 |  | $2.72
Capacitor | Yageo CC0603JRNPO9BN200 | C15,C16,C17,C18 | 20pF | link (https://www.digikey.com/product-detail/en/yageo/CC0603JRNPO9BN200/311-1424-1-ND/2833730) | DigiKey | 311-1424-1-ND | 0.1 | 4 | 0.4 | 8 |  | $0.80
Resistor | Yageo RC0603JR-071KL | R1,R2,R3,R4,R6,R7 | 1KOhm | link (https://www.digikey.com/product-detail/en/RC0603JR-071KL/311-1.0KGRCT-ND/729624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) | DigiKey | 311-1.0KGRCT-ND | 0.1 | 4 | 0.4 | 8 |  | $0.80
Resistor | Vishay TNPW06035K30BEEA | R5,R9 | 5.3KOhm | link (https://www.digikey.com/product-detail/en/TNPW06035K30BEEA/541-4550-1-ND/9448554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) | DigiKey | 541-4550-1-ND | 0.62 | 2 | 1.24 | 4 |  | $2.48
Resistor | Stackpole Electronics RMCF0603FT13K7 | R8 | 13.7KOhm | link (https://www.digikey.com/product-detail/en/RMCF0603FT13K7/RMCF0603FT13K7CT-ND/5049742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) | DigiKey | RMCF0603FT13K7CT-ND | 0.1 | 1 | 0.1 | 2 |  | $0.20
Resistor | Stackpole Electronics RMCF0603FT133K | R10 | 133KOhm | link (https://www.digikey.com/product-detail/en/RMCF0603FT133K/RMCF0603FT133KCT-ND/4425058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) | DigiKey | RMCF0603FT133KCT-ND | 0.1 | 1 | 0.1 | 2 |  | $0.20
Fuse | Bel Fuse 0ZCH0200FF2E | F1 | 2A @ 6V | link (https://www.digikey.com/product-detail/en/te-connectivity-amp-connectors/4-1734506-3/A115198-ND/2263328) | DigiKey | 507-1792-1-ND | 0.26 | 1 | 0.26 | 2 |  | $0.52

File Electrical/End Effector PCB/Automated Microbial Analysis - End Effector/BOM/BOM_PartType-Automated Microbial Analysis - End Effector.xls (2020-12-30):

Comment | Description | Designator | Footprint | LibRef | Manufacturer Part Number | Quantity
Samsung CL21A475KAQNNNG | Ceramic capacitor SMD 0805 4.7 µF 25 V 10 % Samsung Electro-Mechanics CL21A475KAQNNNG 3000 pc(s) | C1, C2 | CL21A475KAQNNNG | CMP-cb72032ddab314b5-2 |  | 2.0
JST B6B-PH-K-S(LF)(SN) | PH Series 6 Position 2 mm Pitch Through Hole Crimp Top Entry Shrouded Header | P1 | PCB-zgutn5khdenyh1r5q6qg-1 | CMP-97605e697e2e48a7-2 | B6B-PH-K-S(LF)(SN) | 1.0
Rohm RK7002BMT116 | N-Channel 60 V 0.2 W Surface Mount 2.5 V Drive Silicon Power Mosfet - SOT-23 | Q1, Q2, Q3, Q4 | PCB-lhick5qix2l1q5xknwuk-1 | CMP-c6120e73f56f19d5-4 |  | 4.0
Res2 | Res Thick Film 0603 10K Ohm 5% 1/10W ±100ppm/°C Molded SMD SMD Paper T/R | R1, R2, R3, R4, R5, R6, R7, R8 | PCB-wz0gdj29sqhj23xvqg5w-1 | CMP-494d8056daa7968a-25 |  | 8.0
STMicroelectronics VL53L1CXV0FY/1 | VL53L1X Series 3.5 V New Generation Long Distance Ranging Time-of-Flight Sensor | U1 | PCB-i0ofxptgesccf2psvnpf-1 | CMP-646fa835e915bba8-9 |  | 1.0
LD1117S33CTR | Fixed Low Drop Positive Voltage Regulator, 3.3V, 4-Pin SOT-223, Tape and Reel | U2 | SOT-223_N | CMP-1170392-2 | LD1117S33CTR | 1.0

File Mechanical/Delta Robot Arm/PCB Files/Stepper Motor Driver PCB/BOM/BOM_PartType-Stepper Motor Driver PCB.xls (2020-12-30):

Comment | Description | Designator | Footprint | LibRef | Manufacturer Part Number | Quantity
0.0022uF | Cap Ceramic 0.0022uF 50V X7R 10% SMD 0805 125C Paper T/R | C7 | CAPC2013X145X50NL20T25 | CMP-8752370-2 | C0805C222K5RACTU | 1.0
0.01uF | Cap Ceramic 0.01uF 50V X7R 20% SMD 0603 125C Paper T/R | C3, C4, C6, C9 | CAPC1608X87X35NL15T15 | CMP-143989-4 | C0603C103M5RACTU | 4.0
0.12 Ohm | Res Thick Film 0603 0.12 Ohm 5% 1/10W ±300ppm/°C Molded SMD Punched Carrier T/R | R4, R5 | PCB-r1zjm8dwx2y0hjgoforr-1 | CMP-21e9ebaea997fe2e-1 | ERJ-3RSJR12V | 2.0
1k Ohm | RC Series 0603 0.1 W 1 kOhms 5% ±100 ppm/°C SMT Thick Film Chip Resistor | R2 | SMD0603GRID25PAD90 | CMP-68a0a2e72c4eb767-17 | RC0603JR-071KL | 1.0
1uF | Cap Ceramic 1uF 50V X5R 10% SMD 0603 85°C Paper T/R | C5 | PCB-hxapk9n2qzqgg8bo7kac-1 | CMP-f7023f64287128c5-2 |  | 1.0
1.1 Ohms | Thick Film Resistors - SMD 1/10watts 1.1ohms 1% | R1 | RESC1608X55X30ML20T10 | CMP-3691192-2 | RK73H1JTTD1R10F | 1.0
2.2uF | Cap Ceramic 2.2uF 50V X5R 10% SMD 0603 85°C Paper T/R | C8 | PCB-by9mfsx1d7doro4kgscm-1 | CMP-8cd4478efca15313-2 | GRM188R61H225KE11D | 1.0
10uF | Cap , mlcc , 1210, 50V , x5R, 10Uf+/-20% , t&r Rohs Compliant: Yes | C1, C2, C10, C11, C12 | PCB-fjsvh2tjaqovriebo4bq-1 | CMP-84d84c8150e65b1f-1 | UMK325BJ106MM-P | 5.0
100k Ohm | RES SMD 100K OHM 0.5% 1/16W 0816 | R3 | RESC1608X50X30LL20T20 | CMP-1864562-2 | RR0816P-104-D | 1.0
150060RS75000 | Standard LEDs - SMD WL-SMCW SMDMono TpVw Waterclr 0603 Red | D1, D2 | PCB-57zpj2ao5h5qcpth1dzy-1 | CMP-12518859-14 |  | 2.0
150060VS75000 | SMD mono-color Chip LED, WL-SMCW, Bright Green | D3, D4 | 0603_A | CMP-12518862-3 | 150060VS75000 | 2.0
Amphenol ICC RJHSE5080 | Connector; Modular Jack; 8; Phosphor Bronze; Gold Over Nickel; 0.62 in. | J1 | PCB-qwl9qjksk46hanrttlea-1 | CMP-cf9c03f44717105b-1 | RJHSE5080 | 1.0
ATtiny25-20PU | 8-bit AVR Microcontroller, 20MHz, 2.7-5.5V, 2KB Flash, 128 Bytes EEPROM, 128 Bytes SRAM, 8-pin PDIP, Industrial Grade (-40°C to 85°C), Pb-Free | U2 | 8P3 | CMP-979084-3 | ATTINY25-20PU | 1.0
Phoenix Contact 1803293 | Wire-To-Board Connector, Right Angle, MC Series, Through Hole, Header, 4, 3.81 mm | J2 | PCB-5cazq4m146w1qodtmxk1-1 | CMP-724734-4 | 1803293 | 1.0
Receptacle_8x1 | Female, 8C, Straight, .100"CC; 3.20mm Tail, No Mt. 100u" Tin; PBT, Phos Bronze, 105 C | J8-L, J8-R | PCB-rk0xvjxtj9hjg7xlxwg2-1 | CMP-674378-7 | PPTC081LFBN-RC | 2.0
Res2 | Surface Mount Thick Film Resistor, Crg Series, 330 Ohm, 200 Mw, - 1%, 50 V, 0603 [1608 Metric] | R6, R7, R8 | PCB-6qp2qqoyvohxfj5se87m-1 | CMP-b10479cbe7db6ec3-1 | CRGH0603F330R | 3.0
SYM-215ae841c9affe9d-1 | Res Thin Film 0805 0.01 Ohm 5% 0.25W(1/4W) 0ppm/C to 350ppm/C Pad SMD Automotive T/R | R10 | PCB-c9ymia8zt8m1a3msw1jq-1 | CMP-1864855-3 | RL1220T-R010-J | 1.0
TE Connectivity / AMP 5747844-4 | Connector D-Subminiature Receptacle 9 Position 2.74mm Solder Right Angle Through Hole 9 Terminal 1 Port Tray | J3 | PCB-0njr3notfioafbnn7qbr-1 | CMP-caba01e9819a157d-5 |  | 1.0
Texas Instruments LMZM23601V5SILT | 36-V, 1-A Step-Down DC-DC Power Module in 3.8-mm × 3-mm Package 10-uSiP -40 to 125 | X1 | PCB-et9mmr8vzuf9nkg2ck12-1 | CMP-08fcc4b6f580d73b-3 |  | 1.0
Trinamic TMC2209-LA-T | Motor Driver, Stepper, QFN-28 | U1 | QFN50P500X500X85_HS-29N | CMP-333afc2d4935ecfd-4 | TMC2209-LA-T | 1.0
Vishay RCP0603B1K60GEA | Res Thkflm Alum Nitride 0603 1.6K Ohm 2% 100PPM Std Term SMD | R9 | PCB-ajdzuyhj1ll9rvlulscs-1 | CMP-b43f7909d1316bf8-1 | RCP0603B1K60GEA | 1.0
Würth Elektronik 61300211121 | THT Vertical Pin Header WR-PHD, Pitch 2.54 mm, Single Row, 2 pins | J5, J6, J7, J9 | PCB-omgsbkhp90n7lpri88og-1 | CMP-748fbcb73d6bab48-27 | 61300211121 | 4.0
XT30 | High Quality Gold Plated XT30 Male Female Bullet Connector | J4 | PCB-qcnpj6p0hbzpl0cja5hs-1 | CMP-9e1652bfce1041d1-4 | FIT0586 | 1.0

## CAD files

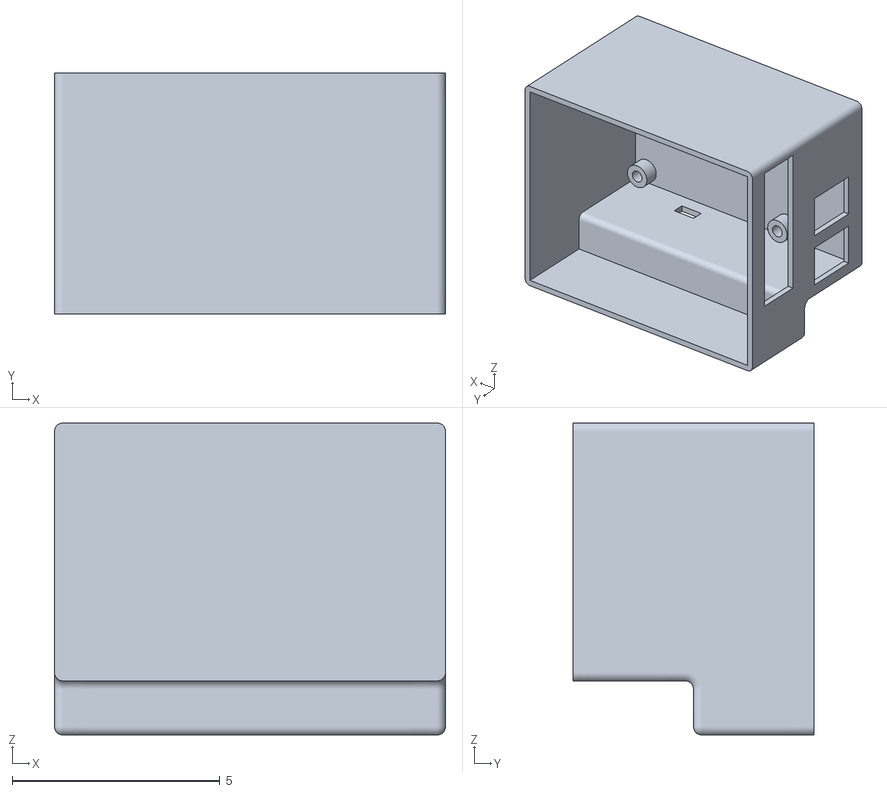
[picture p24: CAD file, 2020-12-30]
Mechanical/Project Model Files/Inventor Files/Custom_Delta/MainPCB_RPI_Case.stl
9.40 x 5.80 x 7.50

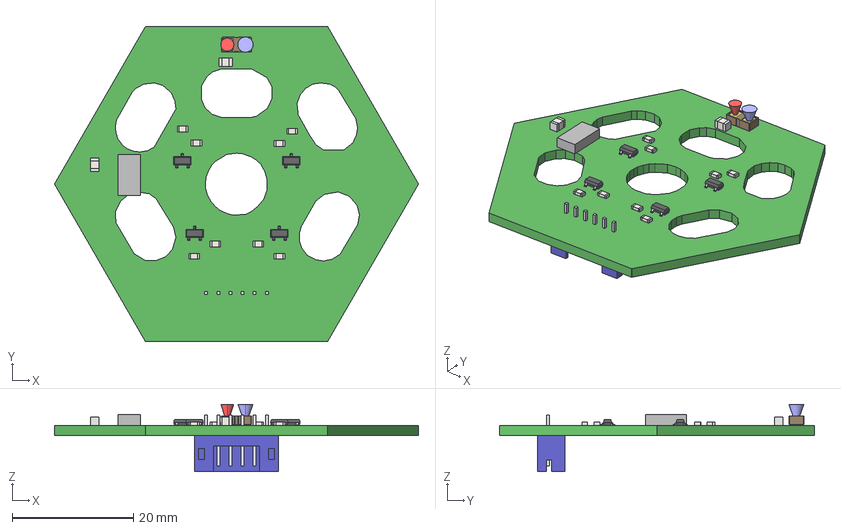
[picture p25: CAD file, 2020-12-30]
Electrical/End Effector PCB/Automated Microbial Analysis - End Effector/ExportSTEP/End_Effector.step
60.1 x 52.1 x 11.1 mm
Board
Extruded x 31
User_Library-vl53l1x_KEEPOUTS
SOT_23 x 4
B6B-PH-K-S

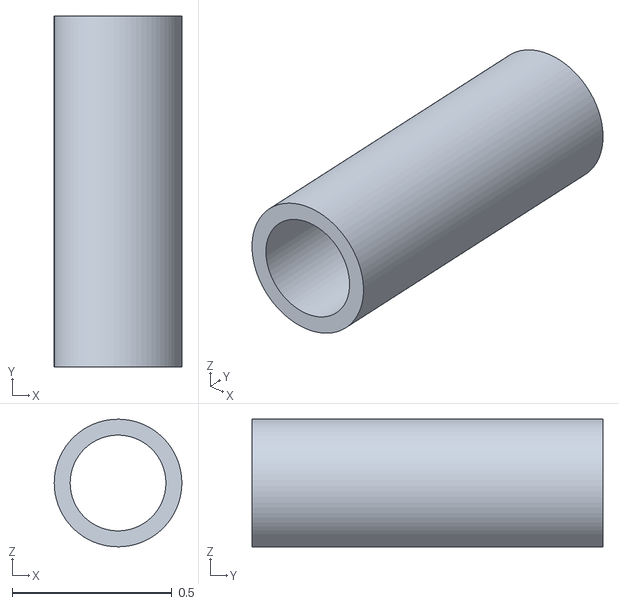
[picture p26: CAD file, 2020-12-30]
Mechanical/Project Model Files/Inventor Files/Custom_Delta/11mmSpacer.stl
0.4 x 1.10 x 0.4

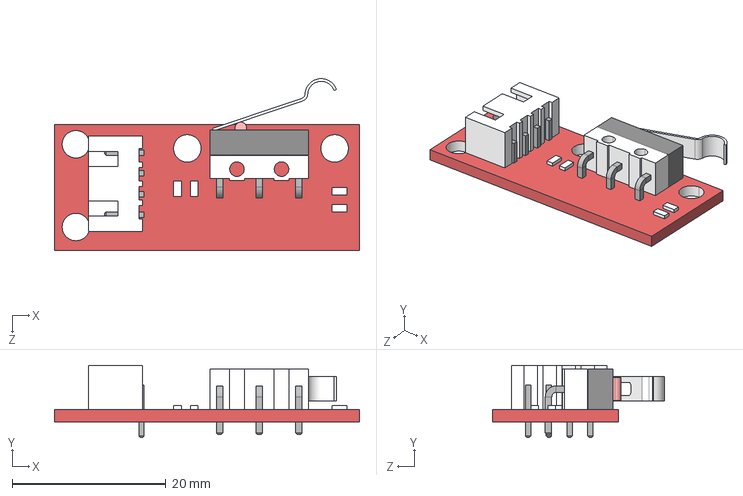
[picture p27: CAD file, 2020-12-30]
Mechanical/Project Model Files/Inventor Files/Limit Switch PCB Model/Switch.STEP
39.7 x 9.40 x 22.4 mm

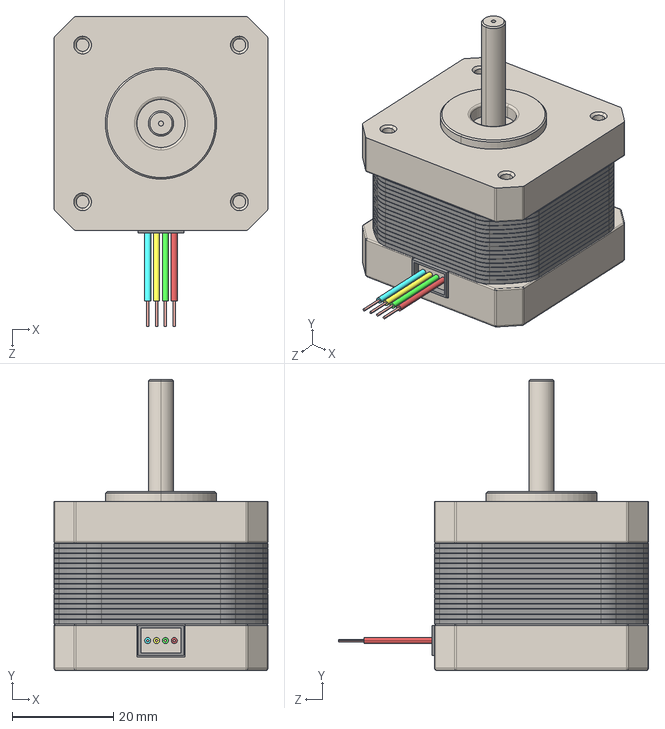
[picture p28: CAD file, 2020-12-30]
Mechanical/Project Model Files/Inventor Files/NEMA17 Motor Model/Nema 17 Stepper Motor length 34mm.STEP
42.3 x 57.6 x 61.3 mm

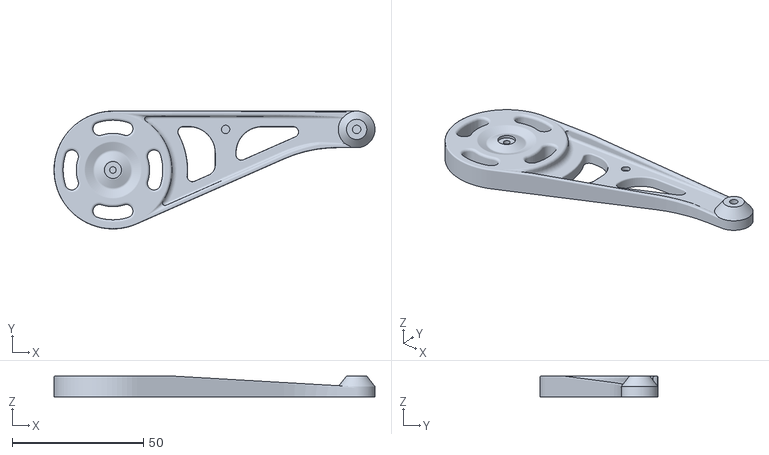
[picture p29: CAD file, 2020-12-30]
Mechanical/Project Model Files/Inventor Files/Reference Delta/EBD.01.02.004_sx_arm.STL
122.5 x 45.0 x 8.00

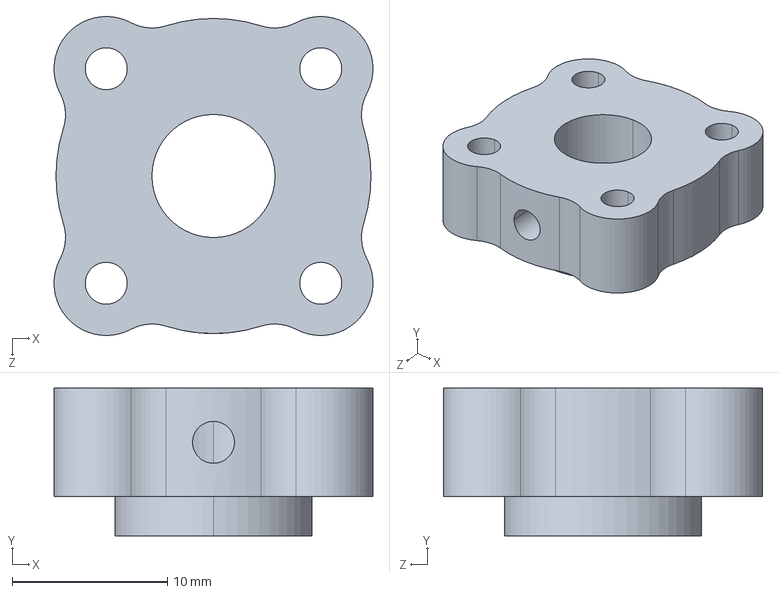
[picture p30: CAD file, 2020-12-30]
Mechanical/Project Model Files/Inventor Files/SparkFun Files/Stepper_Collar/products/12196/step/model.step
20.6 x 9.53 x 20.6 mm

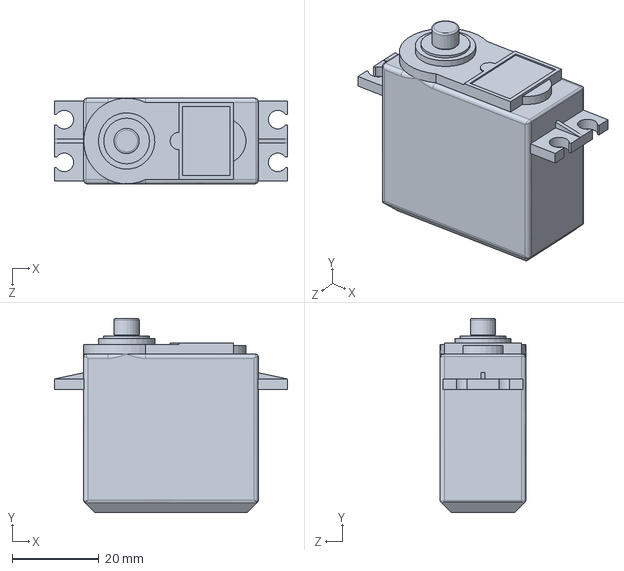
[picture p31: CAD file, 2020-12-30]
Mechanical/Project Model Files/Inventor Files/SparkFun Files/towerpro-mg995 Servo/kiso.SLDPRT
53.8 x 44.8 x 19.8 mm

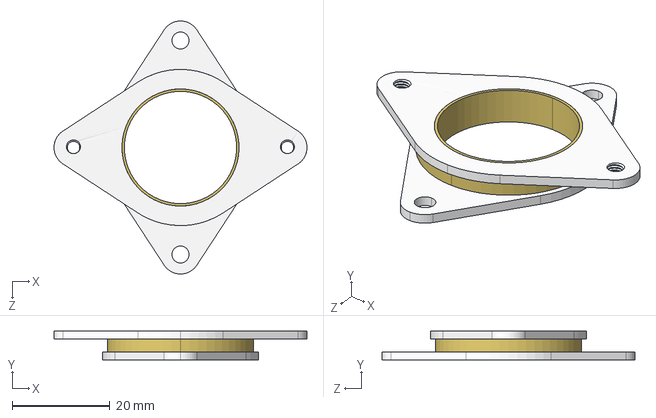
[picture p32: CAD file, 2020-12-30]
Mechanical/Project Model Files/Inventor Files/NEMA17 Motor Model/Nema 17 Damper V2.STEP
51.8 x 5.90 x 51.8 mm

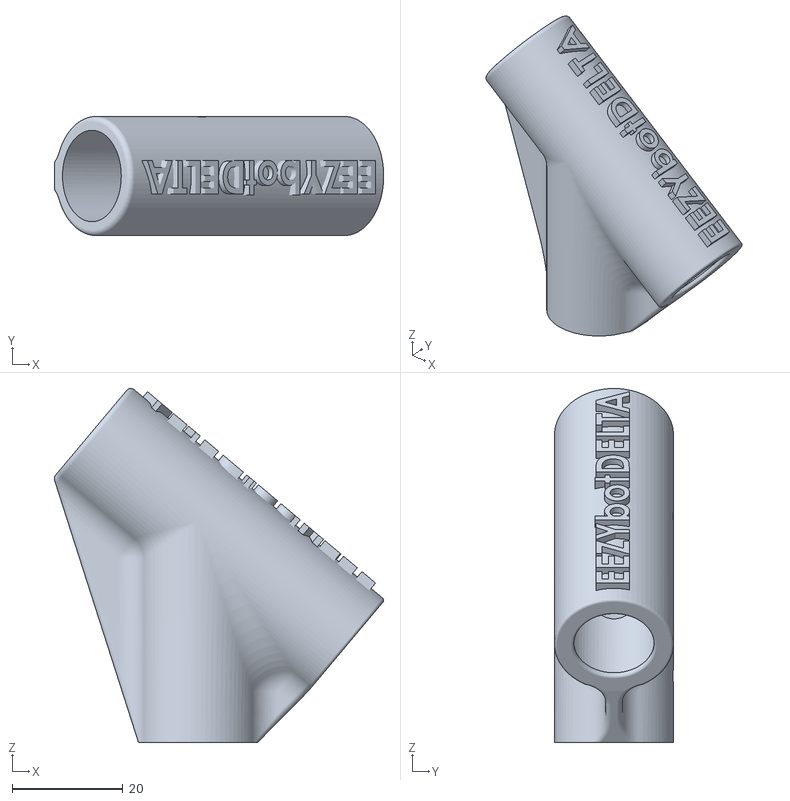
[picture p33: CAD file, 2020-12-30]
Mechanical/Project Model Files/Inventor Files/Reference Delta/EBD.01.01.003_corner.STL
59.5 x 21.5 x 63.9

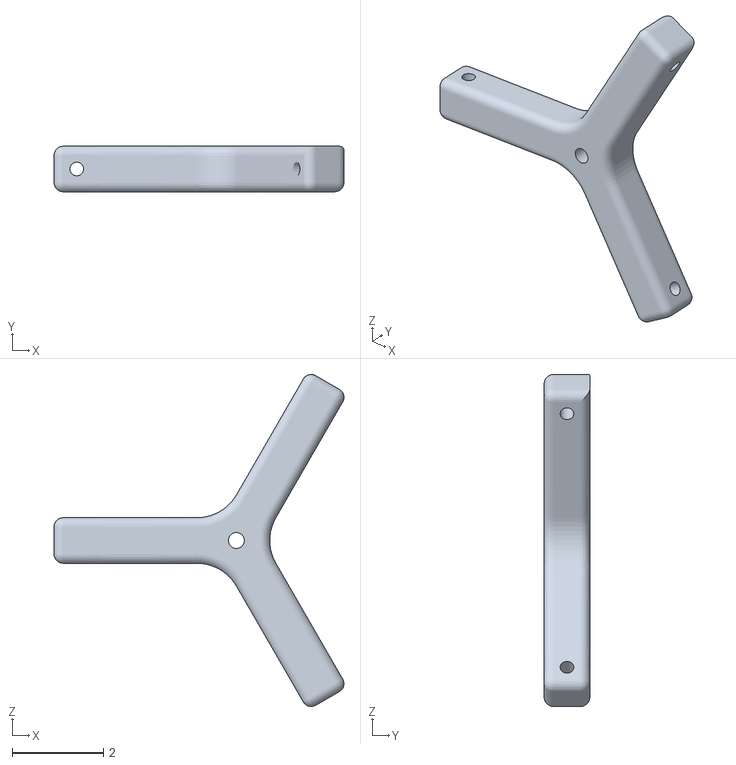
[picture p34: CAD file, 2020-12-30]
Mechanical/Project Model Files/Inventor Files/Custom_Delta/Custom_Delta_End_Effector.stl
6.36 x 1.00 x 7.28

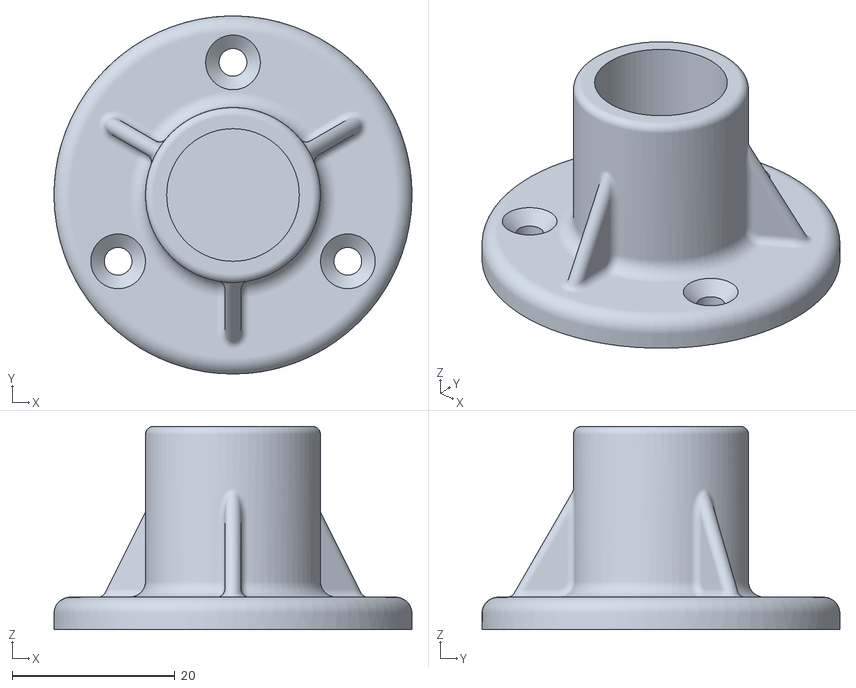
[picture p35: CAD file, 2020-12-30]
Mechanical/Project Model Files/Inventor Files/Reference Delta/EBD.01.02.006_feet.STL
44.0 x 44.0 x 25.0

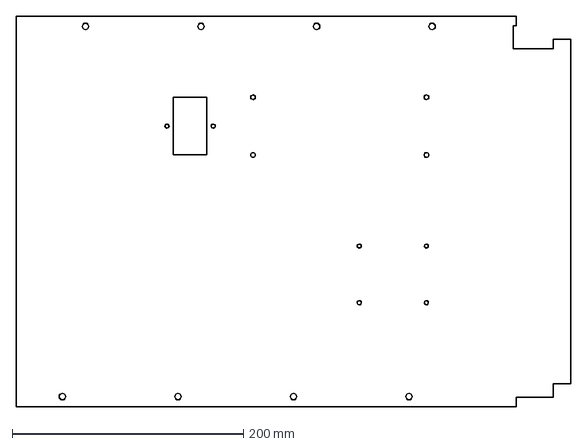
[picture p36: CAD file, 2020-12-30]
Mechanical/Project Model Files/Inventor Files/Custom_Delta/Acrylic_Panel_,mounts.dxf
480.0 x 337.8 mm

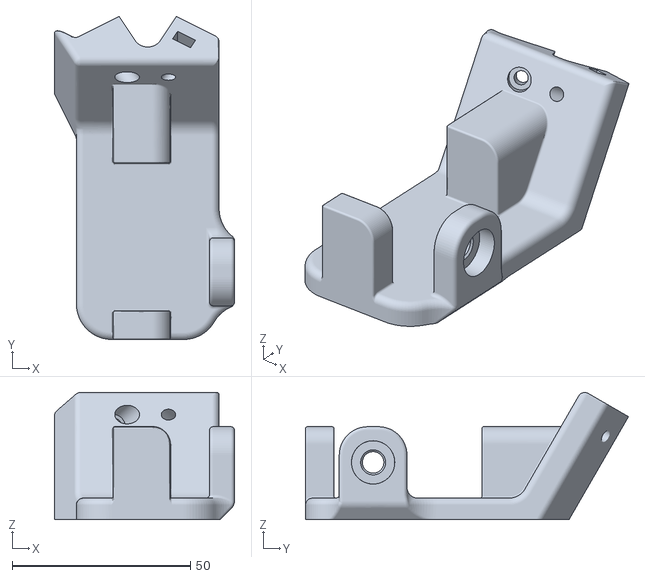
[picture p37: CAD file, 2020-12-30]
Mechanical/Project Model Files/Inventor Files/Reference Delta/EBD.01.02.001support.STL
50.4 x 90.5 x 35.6

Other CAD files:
Mechanical/Project Model Files/Inventor Files/Custom_Delta/Custom_Delta_Assembly.dwg
Mechanical/Delta Robot Arm/PCB Files/Automated Microbial Analysis - End Effector/ExportSTEP/End_Effector.step
Mechanical/Project Model Files/Inventor Files/SparkFun Files/Stepper_Collar/products/12488/step/model.step
Mechanical/Project Model Files/Inventor Files/Custom_Delta/Rod_constraint.stl
Mechanical/Delta Robot Arm/PCB Files/Automated Microbial Analysis - End Effector/ExportSTEP/1151214544.iam
Mechanical/Delta Robot Arm/PCB Files/Automated Microbial Analysis - End Effector/ExportSTEP/1151214672.iam
Mechanical/Delta Robot Arm/PCB Files/Automated Microbial Analysis - End Effector/ExportSTEP/1151214800.iam
Mechanical/Delta Robot Arm/PCB Files/Automated Microbial Analysis - End Effector/ExportSTEP/1151214928.iam
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

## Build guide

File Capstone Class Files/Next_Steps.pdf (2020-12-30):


ECE 44x - Group 3

Automated Microbial Analysis

# Next Steps Document

## Jorian Bruslind

## Mack Hall

## Zach Bendt

May 22, 2020

## Contents

1 Introduction | 2
2 Next Steps/Improvements | 3

1

Mechanical Design | Automated Microbial Analysis

## Abstract

This document was created to provide information and insight into the final status of the Automated Microbial Analysis Capstone Project (ECE 441 - 443: Team 3). The overall goal of the project was to create an automated system to analyze, sort, and log petrifilm microbial data for Analysis Laboratory. To that end, the team decided to create a delta robot mechanism with a Raspberry Pi 4/Raspberry Pi Camera V2. In the end, the project was left unfinished due to the coronavirus outbreak.

## 1 Introduction

The Automated Microbial Analysis project aims to develop a system which is able to analyze a series of microbial samples on a special media called PetriFilm [?] automatically. This is a 3M product that is used in a variety of scientific capacities, mainly in food science and the medical field.


Figure 1: 3M PetriFilm Single Sample

PetriFilm is a very thin paper-like substance which has 2 layers: on one there is an agar media film that is used to grow bacterium, On the other there is a wax coating that is used to seal the sample from outside interference. A liquid sample can be applied to this agar film and left to incubate over a period of 1 - 2 days. After this time, the bacteria that were present within the sample will have had enough time to grow into colonies which are visible to the human eye. These colonies can be counted and the original number of bacterium per unit volume can be known from the original sample. The process to count the bacteria samples and categorize them into datasets is often tedious and can take a human operator around 1 - 2 minutes per sample [?]. With sample sizes of 50 - 60, this process can easily take over an hour. The goal of our project is to use an automated system to count these bacteria colonies in sample sets of upwards of 100+ in as little as 20 minutes. This data will be automatically stored and tabulated within the client’s original database.

For this process it is necessary to create a physical manipulation system that will be able to move paper-like objects in an efficient and precise manner. These samples are somewhat delicate and require careful handling. In addition, they must be placed in a specific orientation so that the bacterial samples can be easily read by some visual component. Therefore it is necessary to create a mechanical system that can be easily made precise and is able to be used for our intended implementation. In addition, there will be designated areas for loading/unloading of samples so that the overall process requires as little human intervention as possible.

Once the loaded, the system will take over and begin the counting process for each sample. There will be error correction and state information for each portion of the counting cycle to ensure the samples are not damaged and to reduce the chance of a miscount. After the sample has been counted and cataloged, it will be placed into one of two sections designated "Pass" or "Needs Review" where they can be sorted by a human operator.

## 2 Next Steps/Improvements

### 2.1 Mechanical

The mechanical system is almost complete and only requires a few components to be fully functional. There are plenty of aspects that could be improved however.

1. Custom Model Material Upgrades

The mechanical system uses a few custom models that were designed for simplicity/easy integration. These parts are currently made using deposition PLA material made from a 3D printer. One of the goals of this section was to use a professional protoyping firm (such as Shapeways) (https://www.shapeways.com/) to create these custom models with more rigid, precise materials. PLA is a great material for prototyping and providing a proof of concept model for use in the system, but there are many other materials available that can be made lighter, stronger and more precisely than what a 3D printer and PLA can accomplish.

Recommendation

Our recommendation would be to look into contracting with an external company and creating the models out of Nylon 11 or RPU70 plastics. Nylon 11 would be the preferred material due to its superior tensile strength to PLA (PA11) (https://static1.sw-cdn.net/files/cms/oem/eos/PA1101.pdf) and its cheap cost compared to RU70 [1]. RU70 is the best material for this task however as it has the highest tensile strength (1900Mpa RU70 vs 1600Mpa PA11) and highest shore hardness (80 D RU70 vs 75 D PA11) [2] (RU70) (https://v.fastcdn.co/u/c5e6ffd9/40698886-0-RPU-70-TDS.pdf)

2. Better Ball Joint Ends

One of the most important components of the delta robot mechanism is the rotating joints at the end of the upper and lower arms. These joints allow for full rotation in one direction and partial ( 60 deg) rotation in the other directions. This motion allows the end effectors motion to be controlled by the 3 arms while maintaining a parallel configuration to the work surface. The original ball joints purchased were repurposed RC car ball joint and are of low quality. Towards the end of the project we were able to replicate this 3 dimensional rotation using 3D printed parts, but ulitmately the motion is still stiff and unreliable.

Recommendation

Our recommendation for this issue would be to look into purchasing official ball joint ends from a certified supplier such as McMaster Carr or any other fastener vendor. This would allow for more information about the available motion of the component while also giving much better precision/accuracy in the parts provided.

3. Small Pneumatic System

The pneumatic system wasn’t fully implemented due to the issues encountered in spring term. However our initial implementation shows that the pneumatic tubing and suction cup/adapter assembly would be too large for the end effector to properly maintain. Our preliminary testing showed that the end effector was over-burdened and would slightly bend/bow in certain directions due to the weight of the tubing.

Recommendation

Our recommendation would be to find a smaller tube set that still provides the necessary -1.4 bar vacuum while also being small enough to not impact the end effector motion. Another idea would be to add a spring damped system to the end effector and the top center of the robot so the end effector is naturally drawn to the center of the robot (and stays parallel to the workspace).

4. Motor Mount Improvement

The current motor mounting system is sufficient for the application but could be made better by creating a component that encloses more of the motor surface area. The main problem is the motors are exposed and the wires have no mounting management. This is necessary so the wires are moved out of the way of the main mechanism and the overall system looks clean.

Recommendation

Our recommendation would be to modify the existing structure of the motor mounts to enclose the entirety of the motors. These models can also be modified to add wire mounting points so the control/feedback wiring can be structured and kept out of the way.

### 2.2 Electrical

The main difficulties of the electrical subsystem have already been completed. What remains are fairly simple, but nonetheless important, tasks that were not able to be completed due to the global health crisis. The majority of the time spent on the electrical subsystem was spent on custom PCB design and getting the motors to move according to a coordinate format.

1. Relaying True Motor Position

Each Auxiliary Stepper Driver PCB contains an ATtiny85, which reads electrical impulses from an integrated encoder on each stepper motor. Each pulse represents another step taken by the motor, so the true motor position can be accounted for through counting the pulses. The ATtiny85s are currently set to send the position individually, but no information accompanies it to notate which motor is sending the information.

Recommendation

In order to solve this issue, the ATtiny85 must be re-flashed with updated code. The current code can be found here, (https://github.com/Jbruslind/ECE44x_Senior_Design/blob/master/Code/Development/Testing%20Scripts/Attiny_Encoder/Attiny85_Encoder/Attiny85_Encoder.ino) on the project GitHub, which should be modified to send another unique character per motor, so the information can have a unique identifier. Then, the Auxiliary ATmega328 should read and parse the information, and pass it along to the Raspberry Pi via serial communication. If the relayed true motor position is different from the expected position, then the Raspberry Pi should trigger a homing sequence in order to realign the expected and actual motor positions.

2. Accounting for the Size of the Incoming Sample Stack

The user can place an arbitrary number of samples to be processed into our system. Additionally, the incoming sample stack will have a varying height throughout the processing procedure, as the incoming stack will shrink with each passing sample being processed. As such, it is important that the height of the end effector is not too high nor too low when attempting to pick up the next sample from the incoming stack.

Recommendation

Adjusting the height of the end effector will have to take place on the Raspberry Pi, as that is what sends the coordinates for the motor arms to execute. The user already inputs the number of samples to be processed into the GUI at the beginning of every session, so we need to find the height which the incoming stack decreases for one sample. Once we find that, we will know how far down the end effector has to travel in order to be able to pick up the first sample and each subsequent sample thereafter. An easy way to implement this would be to have a set coordinate that places the end effector directly over the incoming stack. After traveling to that coordinate, the end effector will be lowered straight down by a varying amount down onto the stack. Due to the delta configuration, moving the head directly up and down is very easy to implement, as all three motors will move by the same amount. The amount that the head will have to move vertically will be incremented by the height of a single processed sample, after each sample is processed. In theory, this will allow the end effector to always have the appropriate height when taking a sample off the incoming stack. Such code needs to be written and implemented into the coordinate execution routine on the Raspberry Pi.

3. The Homing Sequence

The motors are equipped with incremental encoders, which means that they only relay if the motor moves forwards or backwards, not motor position; once power is lost in the system, so is the motor position. We can know if the motor is moving, but that information is not very valuable if we do not know where the motor arm currently is. The homing sequence remedies this by moving the motors all the way in a single direction until they cannot move any further. Since we know how far each motor can extend, we know where is motor arm is now located. From there, we are able to calculate the motor arm position no matter where it is moved, since we know the initial position and all subsequent movements.

Recommendation

The homing sequenced needs to be implemented. Luckily, the software used to relay motor movement, grbl, (https://github.com/grbl/grbl) has a dedicated command for homing sequences. Once the limit switches are hooked up to their respective Auxiliary Stepper Driver PCB, grbl will take care of the rest. However, the software found on the Main ATmega328, which runs grbl, will have to be modified. Variable $22 holds a boolean value for the homing sequence enable. Currently it is set to 0, but should be set to 1 for grbl to do it automatically on startup. To do this, simply run the code in the Arduino IDE and type "$22=1" into the serial monitor. This will save the variables value even after a power cycle.

4. Minor PCB Improvements

As this project was completed on a strict budget of both time and money, additional revisions of the PCB could not be ordered once small issues were discovered.

Recommendation

The PCBs, if re-manufactured, need to have a few adjustments. On the Auxiliary Stepper Driver PCBs, the output pins for the DB9 encoder connector need to be adjusted. The trace between the ATtiny85 physical pin 2 and the pin for EA- or Pin 4 on the DB9 connector should be removed. Then ATtiny85 physical pin 2 should be connected to the pin for EB+ or Pin 2 on the DB9 connector. This will allow for the encoder to pass on the motor position to the ATtiny85 correctly. On the Central Processing PCB, the 5VDC line for the 5V headers should be modified. Pin 2 of P9 or P10 respectively need to be connected to the 5V supply. Unfortunately, an oversight during designing the PCB lead to these pins being connected to the wrong net, so they are not receiving any power without a jumper currently.

### 2.3 Computer Science

1. Computer Vision Improvements

The computer vision system needs to be improved to increase the accuracy of the counts. This is a critical part of the project and is directly related to engineering requirements. The requirement stated that The system should correctly identify and count the microbial colonies to within a 10% error of a human but ideally, the system should to be as accurate at counting microbial samples as a human eye.

Recommendation The computer vision should be honed using the five parameters that are set in the colonyCounter.py file. The five parameters are intensity threshold, area, circularity, convexity and inertia. These parameters should be set once the testing environment is stable. This is done by mounting LED’s around the camera to make the amount of light on the sample when the image is captured the same for every image. Tuning these parameters before the lighting is stable could lead to imprecise results.

2. Automation Controls Integration

The automation controls are calculated by the RaspberryPi which then sends the control messages via serial interface to the ATmega328 where they are decoded and used to set the motors to the proper angles. These control messages are integrated into the user interface software along with the computer vision software. The functions for the controls have yet to be written.

Recommendation The automation controls functions have already been stubbed out in the robocontrols.py file, which can be found on the GitHub. They currently just print to the console for debugging purposes. They just need to send the proper (x,y,z) coordinates to the ATmega328’s. The encoders on the motors can be used to find the proper coordinates to get the right sequence of motor positions. There may also be some timing issues to work out depending on how long each step of the process will take. This can be easily taken care of by implementing wait() function calls as needed and using trial and error to find the optimum sequence.

3. PefriFilm Size detection

This prototype was made specifically for Analysis Laboratories and There are multiple sizes of petrifilm that can be used to perform the food sample testing. To make the bot more marketable to other companies the bot should be able to adjust the height at which the image is captured. This would require the computer vision system to be able to detect the size of the petrifilm. This is because the camera is mounted on the bottom of the base and the position and focus are fixed.

Recommendation

In order to implement size detection, the range of motion of the end effector could be translated into a size range of the petrifilm based on the field of vision of the camera. There would also need to be edge detection to find the size, in pixels of the circular testing area on the petrifilm which could then be translated into millimeters based on how far away the end effector is from the camera when the image is captured.

4. Gas detection

During one of the initial informational meetings with our client there was a discussion about adding gas detection to the computer vision system. Gas is produced by some of the microbes that grow on the petrifilm and create bubbles under the material that is used to seal the petrifilm. The challenge in adding gas detection to the computer vision analysis would be integrating it with the microbial colony detection while maintaining the accuracy of the basic detection.

Recommendation

To add gas detection would require edge detection to be integrated into the computer vision to detect the bubble around a microbial colony. In addition, there would need to be a separate sorting stack for the samples that are found to have gas bubbles. Any addition to the computer vision portion of the project might also require additional processing power. This could be implemented using a more specialized PCB used in place of the RaspberryPi.

## References

[1] S. Inc., “3D Printing PA11 - Shapeways,” May 2020, [Online; accessed 20. May 2020]. [Online]. Available: https://www.shapeways.com/materials/pa11
[2] “Shapeways + Carbon,” May 2020, [Online; accessed 20. May 2020]. [Online]. Available: https://www.shapeways.com/partnership/carbon#page-block-o067l2oj9l

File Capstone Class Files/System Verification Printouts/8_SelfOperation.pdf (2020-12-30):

Requirement: | --Make a Selection-- | Submit
Short Name: 8. Self-operation
Client Requirement: The system requires limited user interaction.
Engineering Requirement: The system will not require user interaction during sample analysis

Think about: What is the intention of this ER? Why is it here and important? What is the bare minimum that could be shown to prove the ER exactly as written even if it is not in the spirit of the ER?
Notes:
Verification Method: Demonstration | Does the verification process adhere to the white box / black box expectations for the verification type? Notes:
Testing Process: The system will not require user interaction during sample analysis | Are the steps clear to you? Assume you had to do this without one of the project team members to help you. Could you do it? Notes:
Test Pass Condition: The system will not require user interaction during sample analysis | Does the test pass condition/process prove the ER as the ER is written? Notes:

General Notes:

System Verification Workshop Printable Template | http://eecs.oregonstate.edu/capstone/ece/student/systemverificationworkshop.php
1 of 1 | 2/19/2020, 7:17 PM

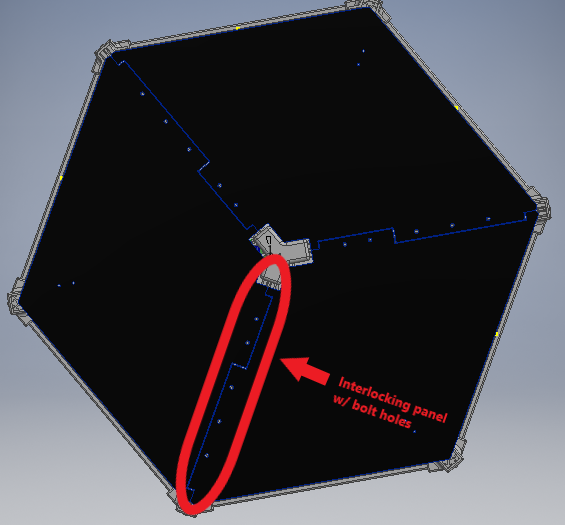
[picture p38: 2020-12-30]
Capstone Class Files/Pictures/Mech Pictures/Custom_Delta_Assembly_Top.png

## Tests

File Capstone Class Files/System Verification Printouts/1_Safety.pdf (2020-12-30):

Requirement: | --Make a Selection-- | Submit
Short Name: 1. Safety
Client Requirement: The system should be safe.
Engineering Requirement: The system enclosure will not allow any object with a diameter greater than 2mm to enter the enclosure.

Think about: What is the intention of this ER? Why is it here and important? What is the bare minimum that could be shown to prove the ER exactly as written even if it is not in the spirit of the ER?
Notes:
Verification Method: Inspection | Does the verification process adhere to the white box / black box expectations for the verification type? Notes:

Testing Process: The system enclosure will not allow any object with a diameter greater than 2mm to enter the enclosure.

Are the steps clear to you? Assume you had to do this without one of the project team members to help you. Could you do it?
Notes:

Test Pass Condition: The system enclosure will not allow any object with a diameter greater than 2mm to enter the enclosure.

Does the test pass condition/process prove the ER as the ER is written?
Notes:

General Notes:

System Verification Workshop Printable Template | http://eecs.oregonstate.edu/capstone/ece/student/systemverificationworkshop.php
1 of 1 | 2/19/2020, 7:13 PM

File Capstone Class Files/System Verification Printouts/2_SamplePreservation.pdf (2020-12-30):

Requirement: | --Make a Selection-- | Submit
Short Name: 2. Sample Preservation
Client Requirement: The system should preserve the samples
Engineering Requirement: The system will not damage the samples | Think about: What is the intention of this ER? Why is it here
and important? What is the bare minimum that could be shown to prove the ER exactly as written even if it is not in the spirit of the ER?
Notes:
Verification Method: Test | Does the verification process adhere to the white box / black box expectations for the verification type? Notes:
Testing Process: The system will not damage the samples | Are the steps clear to you? Assume you had to do this without one of the project team members to help you. Could you do it? Notes:
Test Pass Condition: The system will not damage the samples | Does the test pass condition/process prove the ER as the ER is written? Notes:

General Notes:

System Verification Workshop Printable Template | http://eecs.oregonstate.edu/capstone/ece/student/systemverificationworkshop.php
1 of 1 | 2/19/2020, 7:15 PM

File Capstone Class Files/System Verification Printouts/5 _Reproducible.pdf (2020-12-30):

Requirement: | --Make a Selection-- | Submit
Short Name: 5. Reproducible
Client Requirement: The system results should be reproducible
Engineering Requirement: The system will produce the same microbial count 9/10 times for the same sample set of 10 test samples

Think about: What is the intention of this ER? Why is it here and important? What is the bare minimum that could be shown to prove the ER exactly as written even if it is not in the spirit of the ER?
Notes:
Verification Method: Test | Does the verification process adhere to the white box / black box expectations for the verification type? Notes:

Testing Process: The system will produce the same microbial count 9/10 times for the same sample set of 10 test samples

Are the steps clear to you? Assume you had to do this without one of the project team members to help you. Could you do it?
Notes:

Test Pass Condition: The system will produce the same microbial count 9/10 times for the same sample set of 10 test samples

Does the test pass condition/process prove the ER as the ER is written?
Notes:

General Notes:

System Verification Workshop Printable Template | http://eecs.oregonstate.edu/capstone/ece/student/systemverificationworkshop.php
1 of 1 | 2/19/2020, 7:16 PM

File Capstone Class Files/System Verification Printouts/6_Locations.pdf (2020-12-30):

Requirement: | --Make a Selection-- | Submit
Short Name: 6. Locations
Client Requirement: The system should be usable in multiple lab environments. Engineering Requirement: The system will operate on the ANSI C84.1-2011 standard voltages

Think about: What is the intention of this ER? Why is it here and important? What is the bare minimum that could be shown to prove the ER exactly as written even if it is not in the spirit of the ER?
Notes:
Verification Method: Inspection | Does the verification process adhere to the white box / black box expectations for the verification type? Notes:
Testing Process: The system will operate on the ANSI C84.1-2011 standard voltages | Are the steps clear to you? Assume you had to do this without one of the project team members to help you. Could you do it? Notes:

Test Pass Condition: The system will operate on the ANSI C84.1-2011 standard voltages Does the test pass condition/process prove the ER as the ER is written?
Notes:

General Notes:

System Verification Workshop Printable Template | http://eecs.oregonstate.edu/capstone/ece/student/systemverificationworkshop.php
1 of 1 | 2/19/2020, 7:16 PM

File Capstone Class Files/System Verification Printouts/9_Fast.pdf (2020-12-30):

Requirement: | --Make a Selection-- | Submit
Short Name: 9. Fast
Client Requirement: The system should work quickly.
Engineering Requirement: The system should be able to process more than 5 samples per minute.

Think about: What is the intention of this ER? Why is it here and important? What is the bare minimum that could be shown to prove the ER exactly as written even if it is not in the spirit of the ER?
Notes:
Verification Method: Test | Does the verification process adhere to the white box / black box expectations for the verification type? Notes:

Testing Process: The system should be able to process more than 5 samples per minute. Are the steps clear to you? Assume you had to do this without one of the project team members to help you. Could you do it?
Notes:

Test Pass Condition: The system should be able to process more than 5 samples per minute.

Does the test pass condition/process prove the ER as the ER is written?
Notes:

General Notes:

System Verification Workshop Printable Template | http://eecs.oregonstate.edu/capstone/ece/student/systemverificationworkshop.php
1 of 1 | 2/19/2020, 7:17 PM

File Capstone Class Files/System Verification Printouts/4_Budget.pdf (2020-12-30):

Requirement: | --Make a Selection-- | Submit
Short Name: 4. Budget
Client Requirement: The system should be on or under budget.
Engineering Requirement: The system should be cost less than $500 to build. | Think about: What is the intention of this ER? Why is it here
and important? What is the bare minimum that could be shown to prove the ER exactly as written even if it is not in the spirit of the ER?
Notes:
Verification Method: Analysis | Does the verification process adhere to the white box / black box expectations for the verification type? Notes:
Testing Process: The system should be cost less than $500 to build. | Are the steps clear to you? Assume you had to do this without one of the project team members to help you. Could you do it? Notes:
Test Pass Condition: The system should be cost less than $500 to build. | Does the test pass condition/process prove the ER as the ER is written? Notes:

General Notes:

System Verification Workshop Printable Template | http://eecs.oregonstate.edu/capstone/ece/student/systemverificationworkshop.php
1 of 1 | 2/19/2020, 7:16 PM

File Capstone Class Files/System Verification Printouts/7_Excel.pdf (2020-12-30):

Requirement: | --Make a Selection-- | Submit
Short Name: 7. Excel
Client Requirement: The system should output data in format compatible with Excel.
Engineering Requirement: The system should output analysis results to a .csv file. | Think about: What is the intention of this ER? Why is it here
and important? What is the bare minimum that could be shown to prove the ER exactly as written even if it is not in the spirit of the ER?
Notes:
Verification Method: Inspection | Does the verification process adhere to the white box / black box expectations for the verification type? Notes:
Testing Process: The system should output analysis results to a .csv file. | Are the steps clear to you? Assume you had to do this without one of the project team members to help you. Could you do it? Notes:
Test Pass Condition: The system should output analysis results to a .csv file. | Does the test pass condition/process prove the ER as the ER is written? Notes:

General Notes:

System Verification Workshop Printable Template | http://eecs.oregonstate.edu/capstone/ece/student/systemverificationworkshop.php
1 of 1 | 2/19/2020, 7:17 PM

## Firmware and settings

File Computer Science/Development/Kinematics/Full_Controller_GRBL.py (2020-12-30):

# -*- coding: utf-8 -*-
"""
Created on Wed May  6 12:09:49 2020

@author: Jorian Brusind
"""
import pygame

import math

import serial
import time

clamp = lambda n, minn, maxn: max(min(maxn, n), minn)

# Open grbl serial port
s = serial.Serial('COM7',115200, timeout=.01) #COM port should be whatever the GRBL reciever is on

#____________________________Kinematics Setup_____________________________________
th1 = th2 = th3 = 90

x = y = z = 0

e = 41 #End effector radius (mm)
f = 102 #Base radius (mm)
re = 332 #Lower arm length (mm)
rf = 210 #Upper arm length (mm)

#Limits are calculated as x = -142.557 -> 142.557
# y = -142.557 -> 142.557
# z = -473.775 - -188.661

#When all motors are 0 deg then the coordinates are (0,0,-241.698)

sqrt3 = pow(3, 1/2)


sleep_t = .75

def delta_calcAngleYZ(x,y,z):
    y1 = -0.5 * .57735 * f
    y = y - (.5 * .57735 * e)
    
    a = (x*x + y*y + z*z +rf*rf - re*re - y1*y1)/(2*z);
    b = (y1-y)/z;
    
    d = -(a+b*y1)*(a+b*y1)+rf*(b*b*rf+rf)
    if d < 0:
        return [0,-1]
    yj = (y1 - a*b - pow(d,1/2))/(b*b + 1)
    zj = a +b*yj
    
    theta = 180.0*math.atan(-zj/(y1-yj))/math.pi
    
    return theta, 0

def delta_calcInverse(x0, y0, z0):
    theta1 = theta2 = theta3 = 0
    theta1, status = delta_calcAngleYZ(x0,y0,z0)
    if status == 0:
        theta2, status = delta_calcAngleYZ(x0*math.cos(2.094) + y0*math.sin(2.094), y0*math.cos(2.094)-x0*math.sin(2.094), z0)
    if status == 0:
        theta3, status = delta_calcAngleYZ(x0*math.cos(2.094) - y0*math.sin(2.094), y0*math.cos(2.094)+x0*math.sin(2.094), z0)
        
    return theta1, theta2, theta3
#____________________________Game Controller Setup_____________________________________
    

pygame.init()

pygame.joystick.init() #Initialize the overall class that controls joysticks

clock = pygame.time.Clock()

clock.tick(20)

usb_controller = pygame.joystick.Joystick(0) #I'm gonna have a stroke reading the docs on this

#Basically you can initalize an actual "Joystick" class which has the ability to do button, axes, and trigger readings
#But for some reason the class is called "Joystick" compared to the parent class "joystick" <- wtf
#Anyway, just remember joystick -> big class, Joystick -> smaller class that has all the attributes we want

#Oh and the 0 is the id of the joystick we want (so depending on the number attached you could grab any of them)
usb_controller.init() #initialize for use

usb_axes = [0] * usb_controller.get_numaxes() #Should be 4 axes (L stick l-r up-down and R stick l-r up-down)

usb_buttons = [0] * usb_controller.get_numbuttons()

# =============================================================================
# A - 0
# B - 1
# X - 2
# Y - 3
# Left bumper - 4
# Right bumper - 5
# back button - 6
# start button - 7
# Left joystick button - 8
# right joystick button - 9
# 
# Axis 0 - Left left/right
# Axis 1 - Left up/down
# Axis 2 - L trig = 1, R trig = -1
# Axis 3 - Right up/down
# Axis 4 - Right left/right
# 
# For joysticks - bottom right make both axes positive
# =============================================================================

start_code = 0

angle1 = angle2 = angle3 = 0
step1 = step2 = step3 = 0
prevstep1 = prevstep2 = prevstep3 = 0

com1 = com2 = com3 = 0


def send_command(x,y,z):
    grbl_command = "G90 G0 " + "X" + str(x) + " Y" + str(y) + " Z" + str(z) + '\n'
    s.write(grbl_command.encode())
    print(s.readline().strip())
# Wake up grbl
s.write(str.encode("\r\n\r\n"))
time.sleep(2)   # Wait for grbl to initialize 
s.flushInput()  # Flush startup text in serial input

#Let x be controlled by axis 3, y axis 4 and z axis 2
while 1:
    pygame.event.get() #VERY IMPORTANT (handles any new events) basically it updates the controller values by checking 
    #if anything changed
    
    axes = usb_controller.get_numaxes()

    for i in range(axes):
        usb_axes[i] = usb_controller.get_axis(i)
    
    buttons = usb_controller.get_numbuttons()
    
    for i in range(buttons):
        usb_buttons[i] = usb_controller.get_button(i)
    
    if usb_buttons[7] == 1:
        break
    if usb_buttons[6] == 1:
        start_code = 1
        
    if start_code:
        com1 += int(usb_axes[3]*5)
        com2 += int(usb_axes[4]*5)
        com3 += int(usb_axes[2]*5)
        com1 = clamp(com1, -130, 130)
        com2 = clamp(com2, -130, 130)
        com3 = clamp(com3, -475, -190)
        angle1, angle2, angle3 = delta_calcInverse(com1, com2, com3);
        #print(angle1, angle2, angle3)
        step1 = int(1600/360 * angle1)
        step2 = int(1600/360 * angle2)
        step3 = int(1600/360 * angle3)
        if step1 != prevstep1 or step2 != prevstep2 or step3 != prevstep3:
            grbl_command = "G90 G0 " + "X" + str(step1 * -1) + " Y" + str(step2 *-1) + " Z" + str(step3*-1) + '\n'
            print(grbl_command)
            s.write(grbl_command.encode())
            prevstep1 = step1
            prevstep2 = step2
            prevstep3 = step3
            print(s.readline().strip())
            time.sleep(.03)
#        send_command(10,-97,120)
#        time.sleep(sleep_t)
#        send_command(-152,-65,145)
#        time.sleep(sleep_t)
#        send_command(-111,146,-72)
#        time.sleep(sleep_t)
#        send_command(43,102,-111)
#        time.sleep(sleep_t)
#        send_command(117,-76,10)
#        time.sleep(sleep_t)
#        send_command(21,52,45)
#        time.sleep(sleep_t)
#        send_command(-29,-3,-9)
#        time.sleep(sleep_t)
#        send_command(51,86,79)
#        time.sleep(sleep_t)
#        send_command(-29,-3,-9)
#        time.sleep(sleep_t * 10)
        
s.close()
        
    
    

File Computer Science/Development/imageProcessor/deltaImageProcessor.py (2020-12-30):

import colonyCounter
import time
import csv
import picamera

camera = picamera.PiCamera()         #initalize camera

SAMPLE_CNT = 0                       #initalize number of samples
CUR_SAMPLE = 0                       #sample number of current sample
COL_COUNT = 0                        #number of colonies found
DATA_ARRAY = [" " for i in range(5)] #array that holds data for output to .csv
COL_MAX = 5                          #test threshold
CLI_INFO = "Client1"                 #initalize client info
TEST_RES = ""                        #initalize PASS/FAIL test result 

def imageCapture(imageNumber):
    # sets the camera resolution
    camera.resolution = (1920,1080)
    
    # sets the directory where the image is stored
    fileName = \
        "/home/pi/Documents/deltaImageProcessor/images/"\
        + str(imageNumber) + ".jpg"                       
    
    # takes an image and stores in specified directory fileName
    camera.capture(fileName)

def toCSV(data):
    with open('/home/pi/Documents/deltaImageProcessor/Database/output.csv', 'w') as file:
        data_writer = csv.writer(file, delimiter=',', quotechar='"', quoting=csv.QUOTE_MINIMAL)
        data_writer.writerow('/n')
        data_writer.writerow(data)
        
        
def AnalyzeSample(petriNumber):
    col_count = 0
    imageCapture(petriNumber)
    #perform image analysis.
    col_count = colonyCounter.analyzeImage(petriNumber)
    return col_count
#    if(COL_COUNT < COL_MAX):      #checks number of samples against threshold
#        TEST_RES = "Pass"         #and applies a PASS/FAIL result.
#    else:
#        TEST_RES = "Fail"
        
    #organize data for output
#    DATA_ARRAY = [str(petriNumber), str(COL_COUNT), TEST_RES, CLI_INFO]

#    toCSV(DATA_ARRAY)             #write to .csv file
    

#def startCommand(sampleCount, sampleNum):
#    SAMPLE_CNT = sampleCount
#    CUR_SAMPLE = 0
#    start_time = time.time()    
#if __name__ == '__main__':  
#    for SAMPLE_CNT in range(SAMPLE_CNT, 0, -1):
#        AnalyzeSample(CUR_SAMPLE)
#        CUR_SAMPLE += 1           #increment current sample number
#    print("--- %s seconds ---" % (time.time() - start_time))

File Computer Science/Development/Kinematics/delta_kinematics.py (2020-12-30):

import math
#Physical dimensions (in mm)
e = 72.0                #End triangle
f = 173.205             #Base triangle
re = 300.0              #Forearm length
rf = 210.0              #Bicept length

spd = 0.0005625         #degrees per step at 1/16th microstepping, 3200 steps per revolution

#Trigonometric Constants
sqrt3 = sqrt(3.0)
pi = 3.141592653
sin120 = sqrt3 / 2.0 
cos120 = -0.5
tan60 = sqrt3 
sin30 = 0.5
tan30 = 1/sqrt3

#Forward kinematics: (theta1, theta2, theta3) -> (x0, y0, z0)
#Returned status: 0=OK, -1=non-existing position

def delta_calcForward (theta1, theta2, theta3, x0, y0, z0):
    t = (f - e)*tan30/2
    dtr = pi/180.0
 
    theta1 *= dtr
    theta2 *= dtr
    theta3 *= dtr
 
    y1 = -(t + rf*cos(theta1))
    z1 = -rf*sin(theta1)
 
    y2 = (t + rf*cos(theta2))*sin30
    x2 = y2*tan60
    z2 = -rf*sin(theta2)
 
    y3 = (t + rf*cos(theta3))*sin30
    x3 = -y3*tan60
    z3 = -rf*sin(theta3)
 
    dnm = (y2 - y1)*x3 - (y3 - y1)*x2
 
    w1 = y1*y1 + z1*z1
    w2 = x2*x2 + y2*y2 + z2*z2
    w3 = x3*x3 + y3*y3 + z3*z3
     
    # x = (a1*z + b1)/dnm
    a1 = (z2 - z1)*(y3 - y1) - (z3 - z1)*(y2 - y1)
    b1 = -((w2 - w1)*(y3 - y1)-(w3 - w1)*(y2 - y1))/2.0
 
    # y = (a2*z + b2)/dnm
    a2 = -(z2 - z1)*x3 + (z3 - z1)*x2
    b2 = ((w2 - w1)*x3 - (w3 - w1)*x2)/2.0
 
    # a*z^2 + b*z + c = 0
    a = a1*a1 + a2*a2 + dnm*dnm
    b = 2*(a1*b1 + a2*(b2 - y1*dnm) - z1*dnm*dnm)
    c = (b2 - y1*dnm)*(b2 - y1*dnm) + b1*b1 + dnm*dnm*(z1*z1 - re*re)
  
    # discriminant
    d = b*b - 4.0*a*c
    if (d < 0): 
        return -1 # non-existing po
    else: 
        z0 = -0.5*(b + sqrt(d))/a
        x0 = (a1*z0 + b1)/dnm
        y0 = (a2*z0 + b2)/dnm
        return 0
 
 # inverse kinematics
 # helper functions, calculates angle theta1 (for YZ-pane)
def delta_calcAngleYZ(x0, y0, z0, theta):
     y1 = -0.5 * 0.57735 * f;                # f/2 * tg 30
     y0 -= 0.5 * 0.57735    * e;             # shift center to edge

     # z = a + b*y
     a = (x0*x0 + y0*y0 + z0*z0 +rf*rf - re*re - y1*y1)/(2*z0);
     b = (y1-y0)/z0;

     # discriminant
     d = -(a+b*y1)*(a+b*y1)+rf*(b*b*rf+rf); 
     if (d < 0):
        return -1;                  # non-existing point
     else:
        yj = (y1 - a*b - sqrt(d))/(b*b + 1);   # choosing outer po
        zj = a + b*yj;
        temp = 0
        if(yj>y1):
            temp = 180.0
        else:
            temp = 0.0
        theta = 180.0*atan(-zj/(y1 - yj))/pi + temp;
        return 0;
 
 # inverse kinematics: (x0, y0, z0) -> (theta1, theta2, theta3)
 # returned status: 0=OK, -1=non-existing position
def delta_calcInverse(x0, y0, z0, theta1, theta2, theta3):
    theta1 = theta2 = theta3 = 0;
    status = delta_calcAngleYZ(x0, y0, z0, theta1);
    if(status == 0): 
        status = delta_calcAngleYZ(x0*cos120 + y0*sin120, y0*cos120-x0*sin120, z0, theta2)  # rotate coords to +120 deg
    if(status == 0): 
        status = delta_calcAngleYZ(x0*cos120 - y0*sin120, y0*cos120+x0*sin120, z0, theta3)  # rotate coords to -120 deg
    return status

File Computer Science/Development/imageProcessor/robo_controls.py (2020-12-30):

import time
import GRBL

start_crdnts_up = {} #start coordinates
start_crdnts_dn = {} #start coordinates

pass_crdnts_up = {} #test pass stack
pass_crdnts_dn = {} #test pass stack

fail_crdnts_up = {} #test fail stack
fail_crdnts_dn = {} #test fail stack

camera_cordnts_up = {} #camera locations
camera_cordnts_dn = {} #camera locations


#Controls functions for the delta
sleep_time = 0.5

def turn_on_vacuum():
    print("Turning on vacuum pump")  

def pickup():
    print("Picking up sample...")
    time.sleep(sleep_time)
            
def drop():
    #for x in range(0, SIZE, 1):
        #grblCom1.write(CONT_MAT1[x])
    print("Dropping sample...")
    time.sleep(sleep_time)
            
def move_to_start():
    print("Moving to Start...")
    time.sleep(sleep_time)

def move_to_camera():
    print("Moving to Camera...")
    time.sleep(sleep_time)

def move_to_passed():
    print("Moving to Pass Stack...")
    time.sleep(sleep_time)
    
def move_to_failed():
    print("Moving to Fail Stack...")
    time.sleep(sleep_time)
    
